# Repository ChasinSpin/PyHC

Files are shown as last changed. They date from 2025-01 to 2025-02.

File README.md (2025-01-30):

# PyHC

## Introduction

PyHC is a bare-bones Circuit Python implementation of a hand controller for the OnStepX telescope controller. It's designed to leverage the Adafruit ESP32-S2/S3 Feathers with built in displays and chargers, requiring only a battery, switches and an RJ12 port (hardware connection only). It possible to build a hand controller without needing a PCB or many parts.

PyHC will connect to OnStepX via WiFi or ST4. It's designed to provide common simple functionality on the basis that other functionality is accessed infrequently and can be accomplished via other means.

The code is designed to be simple, so is easy to adapt.  Installation is a breeze, being drag and drop.

If you need to build a controller fast, this is likely the quickest method other than purchasing something ready built.

Although PiHC code is a complete write from scratch, it contains catalogs and algorithms derived from:

* [Smart Hand Controller](https://github.com/hjd1964/SmartHandController)
* [Teen Astro](https://github.com/charleslemaire0/TeenAstro)

## Building The Hardware

| Item | GPIO |
| ---- | ---- |
| F1 | GPIO5 |
| F2 | GPIO6 |
| N | GPIO9 |
| S | GPIO10 |
| E |  GPIO11 |
| W | GPIO12 |
| Center |  GPIO8 (A5) |
| Power Switch | EN(if powered by LiPo), USB(if powered by 5V regulator) |
| Power Switch | GND |

Connect the other side of every button switch to GND

If 3 x AA powered, connect Schottky Diode CUS08F30H3FCT in 4.5V from battery (for reverse polarity protection), and use https://www.amazon.ca/dp/B09Z2CVQYQ 5V Buck Boost Power Module to convert battery to 5V.

## 3D Printed Case

## Installing

1. Connect feather via USB to a desktop
2. If the feather is brand new, i.e. Circuit Python has not been installed yet, then:
	* Enter Bootloader Mode: Press reset, pause 1 second, press reset again to enter the Green/Blue/Orange Feather TFT Bootloader mode.  If you fail to enter this mode, try again.
	* A new drive will be av available on your system called something like FTHRS3BOOT
	* Download the latest version .UF2 for Circuit Python for your board from [Circuit Python Downloads](https://circuitpython.org/downloads), pay particular attention that you download for the correct board type
	* Copy the .uf2 to the FTHRS3BOOT drive
	* Congratuations, you now have Circuit Python installed
3. The board will reset automatically, and a new drive CIRCUITPY will become available
4. Edit src/settings.toml and change to your requirements
5. Copy all the files from src onto the top level of the CIRCUITPY drive
6. The board will auto reset and you're ready to connect to OnStep

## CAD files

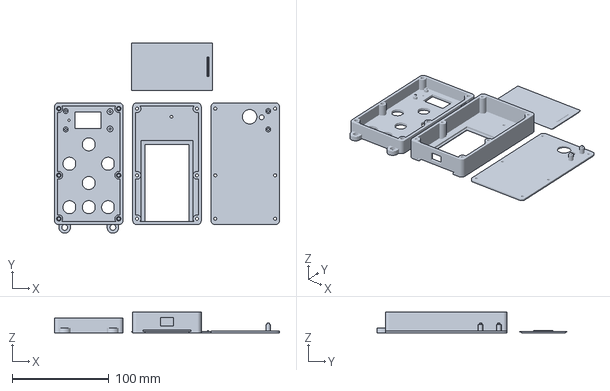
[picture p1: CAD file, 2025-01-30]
case/case.3mf
233.0 x 197.2 x 21.5 mm

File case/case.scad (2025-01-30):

// Print with support (needed for the switch and battery door)
// Need 6 x Hanglife M3 inserts and 6 Counter sunk M3 x 20

partNum                     = 1;        // 0 = All assembled, 1 = All ready for printing, 2 = bottom, 3 = top, 4 = Battery base, 5 = batteryDoor

border                      = 3.0;
caseCornerRadius            = 4.0;
caseInsideDimensions        = [65, 120, 31];
caseOutsideDimensions       = [caseInsideDimensions[0] + border * 2, caseInsideDimensions[1] + border * 2, caseInsideDimensions[2] + border * 2];
switchOutsideDiameter       = 18.0;
switchHoleDiameter          = 13.5;
switchLocatorInset          = 0.5;

switchLocationsOffsetY      = 0;
switchLocations             = [ [0, -45], [-20, 0], [20, 0], [0, -20], [0, 20], [-20, -45], [20, -45] ];
biColorButtonsLocations     = [ [-20, 0], [20, 0], [0, -20], [0, 20] ];

caseJoiningPostLocations    = [ [-31, -57], [-31, -12], [-31, 57], [31, -57], [31, -12], [31, 57] ];
caseJoiningPostDiameter     = 8.0;

m3InsertDiameter            = 4.35 + 0.3;
m3InsertDepth               = 5.0;
m3BoltHoleDiameter          = 3.2;
m3BoltHoleDepth             = caseOutsideDimensions[2] / 2 - border;
m3HeadDiameter              = 7.0;
m3HeadHeight                = 2.0;

featherOffset               = [1, 45];
featherDimensions           = [51, 23, 10];
featherDisplayDimensions    = [27, 17, 2];

featherPostHeight           = 2.6 ;
featherBoltPostDiameter     = 6.0;
featherBoltPostHoleDiameter = 2.1;
featherBoltPostHoleDepth    = featherPostHeight + border - 1.0;
featherBoltPostHolePositions= [2.5, 2.5];
featherSupportPostPositions = [2.65, 2.0];
featherSupportPostDiameter  = 5.0;
featherSupportPostPostDia   = 2.2;
featherSupportPostPostHeight= 1.5;

featherSupportMatingDiameter= 2.6;
featherSupportMatingHeight  = 6.4;

mapLEDHoleDiameter          = 3.0;
mapLEDHoleOffset            = [3.55, 3.61];

resetHoleDiameter           = 2.2;
resetHoleOffset             = [19.5, 0];

lanyardInsideHoleDiameter   = 6.0;
lanyardOutsideHoleDiameter  = 12.0;
lanyardHeight               = 5.0;
lanyardLoopOffsetX          = 25;

usbPortDimensions           = [20, 13, 8.6];
usbPortOffsetZ              = 3.36 + 0.3;

caseSplitHeight             = 21.5;
caseTopHeight               = caseSplitHeight;
caseBottomHeight            = caseOutsideDimensions[2] - caseSplitHeight;
caseTopSplitOffsetZ         = 0;
caseBottomOffsetZ           = caseSplitHeight;

boltHeadDepth               = 10.0;

batteryBaseThickness        = 2.0;
batteryBasePwrDiameter      = 5.0;
batteryBasePwrOffsetXY      = [17.0, 48];

biColorRingDiameter         = 20.25;
biColorDepth                = 0.6;
biColorOutsideWidth         = 3.0;

manifoldCorrection          = 0.01;
manifoldCorrection2         = manifoldCorrection * 2;

batterySliderFlangeWidth    = 2.0;
batterySliderDimensions     = [50, 85, border/2 + manifoldCorrection];
batterySliderInnerDimension = [batterySliderDimensions[0] - batterySliderFlangeWidth * 2, batterySliderDimensions[1] - batterySliderFlangeWidth, border/2 + manifoldCorrection2];
batterySliderCaseReinforcementDimensions    = [batterySliderDimensions[0] + batterySliderFlangeWidth * 2, batterySliderDimensions[1] + batterySliderFlangeWidth, batterySliderFlangeWidth];
batteryDoorScaling          = [0.99, 0.99, 0.5];
batteryDoorLocatorDiameter  = batterySliderFlangeWidth;
batteryDoorLocatorWidth     = 20;
batteryDoorLocatorOffsetY   = border + batteryDoorLocatorDiameter/2 - 0.4 + 2.0;
batteryDoorLocatorOffsetZ   = 2.3 - 1.0;
batteryDoorNotchDimensions  = [30, 4, 1];
batteryDoorNotchSpacing     = 7;

powerSwitchDimensions       = [13.25 + 0.3, border + manifoldCorrection2, 8.85 + 0.3];
powerSwitchOffsetZ          = border + 4;



if ( partNum == 0 )
{
    caseBottom();
    caseTop();
}

if ( partNum == 1 )
{
    caseBottom();
    translate( [-caseOutsideDimensions[0] - 10, 0, caseOutsideDimensions[2]] )
        rotate( [0, 180, 0] )
            caseTop();
    translate( [caseOutsideDimensions[0] + 10, 0, 0] )
        batteryBase();
        
    translate( [-15, caseOutsideDimensions[1]/2 + batterySliderDimensions[1]/2 - 5, 0] )
        rotate( [0, 0, 90] )
            batteryDoor();
}

if ( partNum == 2)
    caseBottom();

if ( partNum == 3)
    translate( [-caseOutsideDimensions[0] - 10, 0, caseOutsideDimensions[2]] )
        rotate( [0, 180, 0] )
            caseTop();

if ( partNum == 4)
    batteryBase();

if ( partNum == 5)
    batteryDoor();

            
module caseBottom()
{
    difference()
    {
        case();
        translate( [0, 0, caseBottomHeight / 2 + caseBottomOffsetZ] )
            cube( [caseOutsideDimensions[0]*2 + manifoldCorrection2, caseOutsideDimensions[1]*2 + manifoldCorrection2, caseBottomHeight + manifoldCorrection], center = true ); 
    }    
}



module caseTop()
{
    difference()
    {
        case();
        translate( [0, 0, caseTopHeight / 2 + caseTopSplitOffsetZ - manifoldCorrection] )
            cube( [caseOutsideDimensions[0]*2 + manifoldCorrection2, caseOutsideDimensions[1]*2 + manifoldCorrection2, caseTopHeight + manifoldCorrection], center = true ); 
    }
}



module batteryBase()
{
    difference()
    {
        roundedCube( [caseOutsideDimensions[0], caseOutsideDimensions[1], batteryBaseThickness], radius = caseCornerRadius );
    
        // Bolt holes
        for ( posXY = caseJoiningPostLocations )
            translate( [posXY[0], posXY[1], 0] )
                translate( [0, 0, -manifoldCorrection] )
                    cylinder(d = m3BoltHoleDiameter, h = batteryBaseThickness + manifoldCorrection2, $fn = 40);
                    
        // Map LED Hole
        translate( [featherOffset[0], featherOffset[1], 0] )
            translate( [mapLEDHoleOffset[0], mapLEDHoleOffset[1], -manifoldCorrection] )
                cylinder(d = mapLEDHoleDiameter * 5, h = batteryBaseThickness + manifoldCorrection2, $fn = 40);     
         
        // Power hole
        translate( [batteryBasePwrOffsetXY[0], batteryBasePwrOffsetXY[1], -manifoldCorrection] )
            cylinder(d = batteryBasePwrDiameter, h = batteryBaseThickness + manifoldCorrection2, $fn = 40);
    }
    
        // Posts to push against the back of the board on the non-screwed positions
    featherPostOffset = featherDimensions[1]/2 - featherSupportPostPositions[1];
    translate( [featherOffset[0] + featherDimensions[0]/2 - featherSupportPostPositions[0], featherOffset[1], 0] )
            {
                for ( posY = [featherPostOffset, -featherPostOffset] )
                    translate( [0, posY, 0] )
                    {
                        cylinder(d = featherSupportPostDiameter, h = batteryBaseThickness + 8.25 - 1.5, $fn = 40);
                        cylinder(d = featherSupportMatingDiameter, h = batteryBaseThickness + 8.25, $fn = 40);
                    }
            }

}



module surroundHighlight()
{
    difference()
    {
        roundedCube( [caseOutsideDimensions[0] + manifoldCorrection2, caseOutsideDimensions[1] + manifoldCorrection2, biColorDepth], radius = caseCornerRadius );
        translate( [0, 0, -manifoldCorrection] )
            roundedCube( [caseOutsideDimensions[0] - biColorOutsideWidth*2, caseOutsideDimensions[1] - biColorOutsideWidth*2, biColorDepth + manifoldCorrection2], radius = caseCornerRadius );
    }
}


module biColorButtonRing()
{
    cylinder(d = biColorRingDiameter, h = biColorDepth);
}



module batterySlider()
{
    translate( [-batterySliderDimensions[0] / 2, -caseOutsideDimensions[1]/2, 0] )
    {
        translate( [batterySliderFlangeWidth, 0, -manifoldCorrection] )
            cube( batterySliderInnerDimension );
        translate( [0, 0, border/2] )
            cube( batterySliderDimensions );
    }
}


module batterySliderCaseReinforcement()
{
    translate( [-batterySliderCaseReinforcementDimensions[0] / 2, -caseOutsideDimensions[1]/2, border] )
        difference()
        {
            cube(batterySliderCaseReinforcementDimensions);
            
            translate( [batterySliderFlangeWidth * 2, 0, -manifoldCorrection] )
                cube( [batterySliderInnerDimension[0], batterySliderInnerDimension[1], border + manifoldCorrection2] );
        }
}



module batteryDoor()
{
    difference()
    {
        union()
        {
            scale( batteryDoorScaling )
                batterySlider();
        
            translate( [0, -caseOutsideDimensions[1]/2 + batteryDoorLocatorOffsetY, batteryDoorLocatorOffsetZ] )
                rotate( [0, 90, 0] )
                    cylinder( d = batteryDoorLocatorDiameter, h = batteryDoorLocatorWidth, center = true, $fn = 40);
        }
        
        for ( posY = [0, batteryDoorNotchSpacing, batteryDoorNotchSpacing*2, batteryDoorNotchSpacing*3] )
            translate( [0, -caseOutsideDimensions[1]/2 + batteryDoorNotchSpacing + posY, -0.1] )
                translate( [-batteryDoorNotchDimensions[0]/2, -batteryDoorNotchDimensions[1]/2, 0] )
                    cube( batteryDoorNotchDimensions );
    }
}
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

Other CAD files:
case/case.stl

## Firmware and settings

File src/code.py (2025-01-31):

import os
import time
from display import Display
from connectionManager import ConnectionManager
from buttons import Buttons
from menus import Menus



def read_version():
	""" Read the current version of the software """
	with open('/version.txt') as fp:
		version = fp.readline()
		version = version.rstrip()
		return version
	return None



#
# MAIN
#

# Read the current version of the software
version = read_version()

# Read settings.toml
connection_method	= os.getenv("CONNECTION_METHOD")
onstepx_wifi_ssid	= os.getenv("ONSTEPX_WIFI_SSID")
onstepx_wifi_password	= os.getenv("ONSTEPX_WIFI_PASSWORD")
onstepx_ip_addr		= os.getenv("ONSTEPX_IP_ADDR")
onstepx_port		= os.getenv("ONSTEPX_PORT")
display_color		= os.getenv("DISPLAY_COLOR")
info_text		= os.getenv("INFO_TEXT")

# Start the display
display = Display(version, display_color, info_text)

buttons			= Buttons()
connection_manager	= ConnectionManager(connection_method, onstepx_wifi_ssid, onstepx_wifi_password, onstepx_ip_addr, onstepx_port, debug=False)
menus			= Menus(connection_manager, version, info_text)

connection_manager.connect()

while True:
	if connection_manager.connected():
		# Read Buttons
		(buttonsPressed, buttonsReleased, buttonsHeld) = buttons.process()

		menus.process(buttonsPressed, buttonsReleased, buttonsHeld)
	
		if menus.needs_display:
			print(menus.display_lines)
			display.display_menu(menus.display_lines)
	else:
 		display.display_connecting(connection_method, onstepx_wifi_ssid)
		connection_manager.connect()

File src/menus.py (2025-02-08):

"""

WCO Catalog:
For common targets we really hit the most common Messiers objects and planets and the moon most often. For Messier objects, probably M3, M4, M8, M11, M13, M15, M16, M17, M27, M31, M42, M44, M45, M46, M51, M53, M57, M63, M65, M66, M81, M82, M84, M86, M92, M97, M101, M104, M106. Oooof that might have been more than you were thinking of adding. 😅 feel free to pick your favourites and exclude the rest!
Top 10 would be: 3,11,13,16,27,42,53,57,81,92


	self.menu = [
			menuItemSubmenu('OBJECT LIBRARY', self.menu_objectlibrary)
		    ]

	self.menu_objectlibrary =  [
			menuItemSubmenu('Solar System', self.menu_object_library_catSolarSystem)
			menuItemSubmenu('NGC', self.menu_object_library_catNgc)
			menuItemSubmenu('IC', self.menu_object_library_catIc)
			menuItemSubmenu('Messier', self.menu_object_library_catMessier)
		]

	MENUS = [
		{'name': 'OBJECT LIBRARY', 'view': self.view_object_library, 'menu': None,},	# View object library
	]

Target:
	M57 EX PNEB
	MAG 9.7 SZ 2.5'

  #include "src/catalogs/data/stars.h"           // Catalog of 408 bright stars
  #include "src/catalogs/data/messier.h"         // Charles Messier's famous catalog of 109 DSO's
  #include "src/catalogs/data/caldwell.h"        // The Caldwell (supplement) catalog of 109 DSO's
  #include "src/catalogs/data/ngc.h"             // The New General Catalog of 8154 DSO's
  #include "src/catalogs/data/ic.h"              // The Index Catalog (supplement) of 5400 DSO's



"""


import time
import board
import neopixel
from connectionManager import ConnectionManager
from adafruit_datetime import datetime, timedelta



class menuItemSubmenu():

	def __init__(self, name, submenu, site_manager_only):
		self.name = name
		self.submenu = submenu
		self.site_manager_only = site_manager_only



class menuItemAction():

	def __init__(self, name, confirmation, operation, arg = None):
		self.name = name
		self.confirmation = confirmation
		self.operation = operation
		self.arg = arg


class menuItemView():

	def __init__(self, name, view, arg, update_rate = None):
		self.name = name
		self.view = view
		self.arg = arg
		self.update_rate = update_rate


class menu():

	MAX_MENU_LINES = 3
	
	def __init__(self, menu):
		self.menu		= menu
		self.selected_index 	= 0
		self.selected_lower	= 0
		self.selected_upper	= min(len(self.menu), self.MAX_MENU_LINES)

	def __str__(self):
		return 'menu: selected_index:%d selected_lower:%d selected_upper:%d' % (self.selected_index, self.selected_lower, self.selected_upper)


class Menus():

	MODE_NORMAL			= 0	# Normal mode, displays menu or other information
	MODE_JOYSTICK			= 1	# Takes joystick input

	STATUS_TIMEOUT			= 1.0
	JOYSTICK_RETRANSMIT_TIMEOUT	= 5.0
	


	def __init__(self, connection_manager, pyhc_version, info):
		self.mode		= self.MODE_NORMAL
		self.needs_display	= True
		self.status_changed	= True
		self.joystick_mode	= False
		self.guide_rate		= 9
		self.conman		= connection_manager
		self.pyhc_version	= pyhc_version
		self.info		= info

		self.menu_parking = [
			menuItemAction('PARK', None, self.action_park),
			menuItemAction('UNPARK', ['UNPARK command sent'], self.action_unpark),
		]

		self.menu_tracking = [
			menuItemAction('TRACKING ON', ['TRACKING switched ON', '', 'Press any button to continue'], self.action_trackingon),
			menuItemAction('TRACKING OFF', ['TRACKING switched OFF', '', 'Press any button to continue'], self.action_trackingoff),
		]

		self.menu_trackingrate = [
			menuItemAction('SIDEREAL', ['TRACKING set to SIDEREAL', '', 'Press any button to continue'], self.action_trackingrate, 'sidereal'),
			menuItemAction('LUNAR', ['TRACKING set to LUNAR', '', 'Press any button to continue'], self.action_trackingrate, 'lunar'),
			menuItemAction('KING', ['TRACKING set to KING', '', 'Press any button to continue'], self.action_trackingrate, 'king'),
			menuItemAction('SOLAR', ['TRACKING set to SOLAR', '', 'Press any button to continue'], self.action_trackingrate, 'solar'),
		]

		self.menu_maxslewrate = [
			menuItemAction('NORMAL (4 deg/s)', ['MAX SLEW RATE set to', 'NORMAL(4 deg/s)', '', 'Press any button to continue'], self.action_maxslewrate, 'normal'),
			menuItemAction('COLD WEATHER (2.7 deg/s)', ['MAX SLEW RATE set to', 'COLD WEATHER (2.7 deg/s)', '', 'Press any button to continue'], self.action_maxslewrate, 'coldweather'),
			menuItemAction('SNAIL PACE (2.0 deg/s)', ['MAX SLEW RATE set to', 'SNAIL PACE (2.0 deg/s)', '', 'Press any button to continue'], self.action_maxslewrate, 'snailpace'),
			menuItemAction('INSANE (6.0 deg/s)', ['MAX SLEW RATE set to', 'INSANE (6.0 deg/s)', '', 'Press any button to continue'], self.action_maxslewrate, 'insane'),
		]

		self.menu_maplight = [
			menuItemAction('MAP LIGHT ON', ['MAP LIGHT switched ON', '', 'Press any button to continue'], self.action_maplighton),
			menuItemAction('MAP LIGHT OFF', ['MAP LIGHT switched OFF', '', 'Press any button to continue'], self.action_maplightoff),
		]

		self.menu_admin = [
			menuItemAction('SETPARK', ['CURRENT POSITION IS', 'NOW THE PARK POSITION!', '', 'Press any button to continue'], self.action_setpark),
			menuItemAction('3 STAR ALIGN', None, self.action_3staralign),
		]

		self.main_menu = [
			menuItemSubmenu('PARKING', self.menu_parking, False),
			menuItemAction('SYNC (ALIGN)', ['CURRENT POSITION aligned', 'to CURRENT TARGET', '', 'Press any button to continue'], self.action_sync),
			menuItemAction('SPIRAL SEARCH', None, self.action_spiral_search),
			menuItemView('POSITION', self.view_position, None, 1),
			menuItemSubmenu('TRACKING ON/OFF', self.menu_tracking, False),
			menuItemSubmenu('TRACKING RATE', self.menu_trackingrate, False),
			menuItemSubmenu('MAX SLEW RATE', self.menu_maxslewrate, False),
			menuItemSubmenu('MAP LIGHT', self.menu_maplight, False),
			menuItemView('DATE/TIME', self.view_date_time, None, 1),
			menuItemView('SITE', self.view_site, None, None),
		
			menuItemView('ABOUT', self.view_about, None, None),
			menuItemSubmenu('SITE MANAGER ONLY', self.menu_admin, True),
		]

		self.menu_stack			= []
		self.top_level_menu		= menu(self.main_menu)
		self.current_menu		= self.top_level_menu

		self.last_get_status		= time.monotonic()
		self.last_status = {}
		self.last_3staralign_time	= time.monotonic()
		self.last_active_view_update	= time.monotonic()

		self.periodic_menu_update	= time.monotonic()

		self.display_lines		= []
		self.active_view		= None
		self.active_view_terminate	= None

		self.pixel			= neopixel.NeoPixel(board.NEOPIXEL, 1)

		self.last_joystick_tx		= time.monotonic()


	def __get_status(self):
		now = time.monotonic()

		if now >= self.last_get_status + self.STATUS_TIMEOUT:
			self.last_get_status = now
			rx = self.conman.send_command('GU', reply_expected = True)	# Status
			self.status =  {}

			if rx is None:
				return
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

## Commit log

2025-01-18 First practical version
    [case.3mf, case.scad, case.stl]
2025-01-30 Adding 3d printed case and base functionality
    [case.3mf, case.scad, case.stl]
2025-02-08 Fixing bug for key error
    [menus.py]
